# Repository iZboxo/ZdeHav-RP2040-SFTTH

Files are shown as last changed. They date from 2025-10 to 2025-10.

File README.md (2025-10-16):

# ZdeHav-RP2040-SFTTH
Stepper, fan, thermistor, thermistor and heater. Does it work? I don't know yet. But I hope so.

# What I know is wrong even now lol
BAV99W - has different mounting pads - one is meant for hand soldering, one for machine. Not a hard issue.
SK310A-TP D3, D4 - also different mounting style, this IS BAD. I missed this one. I only found 40V/0.3A schottky in 0603 - AND THATS NOT ENOUGH.

PCB
PCBdesign
Schematic1
Schematic2
PCBTop

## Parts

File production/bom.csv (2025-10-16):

Designator | Footprint | Quantity | Value | LCSC Part #
C1, C36, C4 | 0805 | 3 | 10u
C10, C8 | 0603 | 2 | 1u
C11, C12, C13, C14, C15, C16, C17, C20, C21, C28, C29, C30, C31, C32, C51, C6, C7, C9 | 0603 | 18 | 100n
C18 | CAPAE830X1050N | 1 | 100u
C19 | 1206 | 1 | 10u
C2, C3 | 0603 | 2 | 15p
C22 | 0603 | 1 | 4.7u
C23, C25, C26, C27 | 0603 | 4 | 1n
C24 | 0603 | 1 | 22n
C33, C34 | 0603 | 2 | 22u
C35 | 0603 | 1 | 10u
C5 | 0603 | 1 | C
D1 | SOT-323_SC-70_Handsoldering | 1 | BAV99W
D2, D5 | 0603 | 2 | LED
D3, D4 | 0603 | 2 | SK310A-TP
D6 | D_SOD-523 | 1 | BAT54KFILM
D7 | SOT-323_SC-70 | 1 | BAV99W
IC1 | AP63205WU7 | 1 | AP63205WU-7
J1 | USB421603A | 1 | USB4216-03-A
J10, J2, J9 | PinHeader_1x02_P2.54mm_Vertical | 3 | Conn_01x02
J11 | PinSocket_2x20_P2.54mm_Vertical | 1 | Conn_02x20_Odd_Even
J3 | SHDR4W97P0X254_1X4_1271X660X1143P | 1 | Conn_01x04
J4 | SHDR2W99P0X500_1X2_1001X762X1001P | 1 | 8718
J5, J6 | SHDR2W64P0X254_1X2_737X660X1181P | 2 | Conn_01x02
J7 | SHDR2W99P0X500_1X2_1001X762X1001P | 1 | Conn_01x02
J8 | RHDR3W64P0X254_1X3_1017X660X1194P | 1 | Conn_01x03
L1, L2, L3, L4, L5 | 0603 | 5 | BLM18KG121TN1D
L6 | L_APV_APH0530 | 1 | 6.8u
Q1 | TO-220-3_Horizontal_TabDown | 1 | IRLZ34NPBF
Q2 | SOT-23-3 | 1 | SI2342DS-T1-BE3
R1, R10, R5 | 0603 | 3 | 1k
R11, R14, R15 | 0603 | 3 | 4k7
R12, R13 | 0603 | 2 | 2k37
R16 | 0603 | 1 | 10k
R17, R19 | 0603 | 2 | 100k
R18 | 0603 | 1 | 2k2
R2 | 0603 | 1 | DNF
R20, R21 | 0603 | 2 | 1k8
R3, R4 | 0603 | 2 | 27.4
R6, R7 | 1206 | 2 | 22mili
R8, R9 | 0603 | 2 | 5k1
TH1 | 0402 | 1 | NTCG104LH104JTDS
U1 | QFN-56-1EP_7x7mm_P0.4mm_EP3.2x3.2mm | 1 | RP2040
U2 | SOT-223-3_TabPin2 | 1 | NCP1117-3.3_SOT223
U3 | SOIC-8_5.3x5.3mm_P1.27mm | 1 | W25Q128JVS
U4 | VQFN-28-1EP_5x5mm_P0.5mm_EP3.7x3.7mm_ThermalVias | 1 | TMC2209-LA
Y1 | Crystal_SMD_Abracon_ABM8G-4Pin_3.2x2.5mm | 1 | ABM8-272-T3

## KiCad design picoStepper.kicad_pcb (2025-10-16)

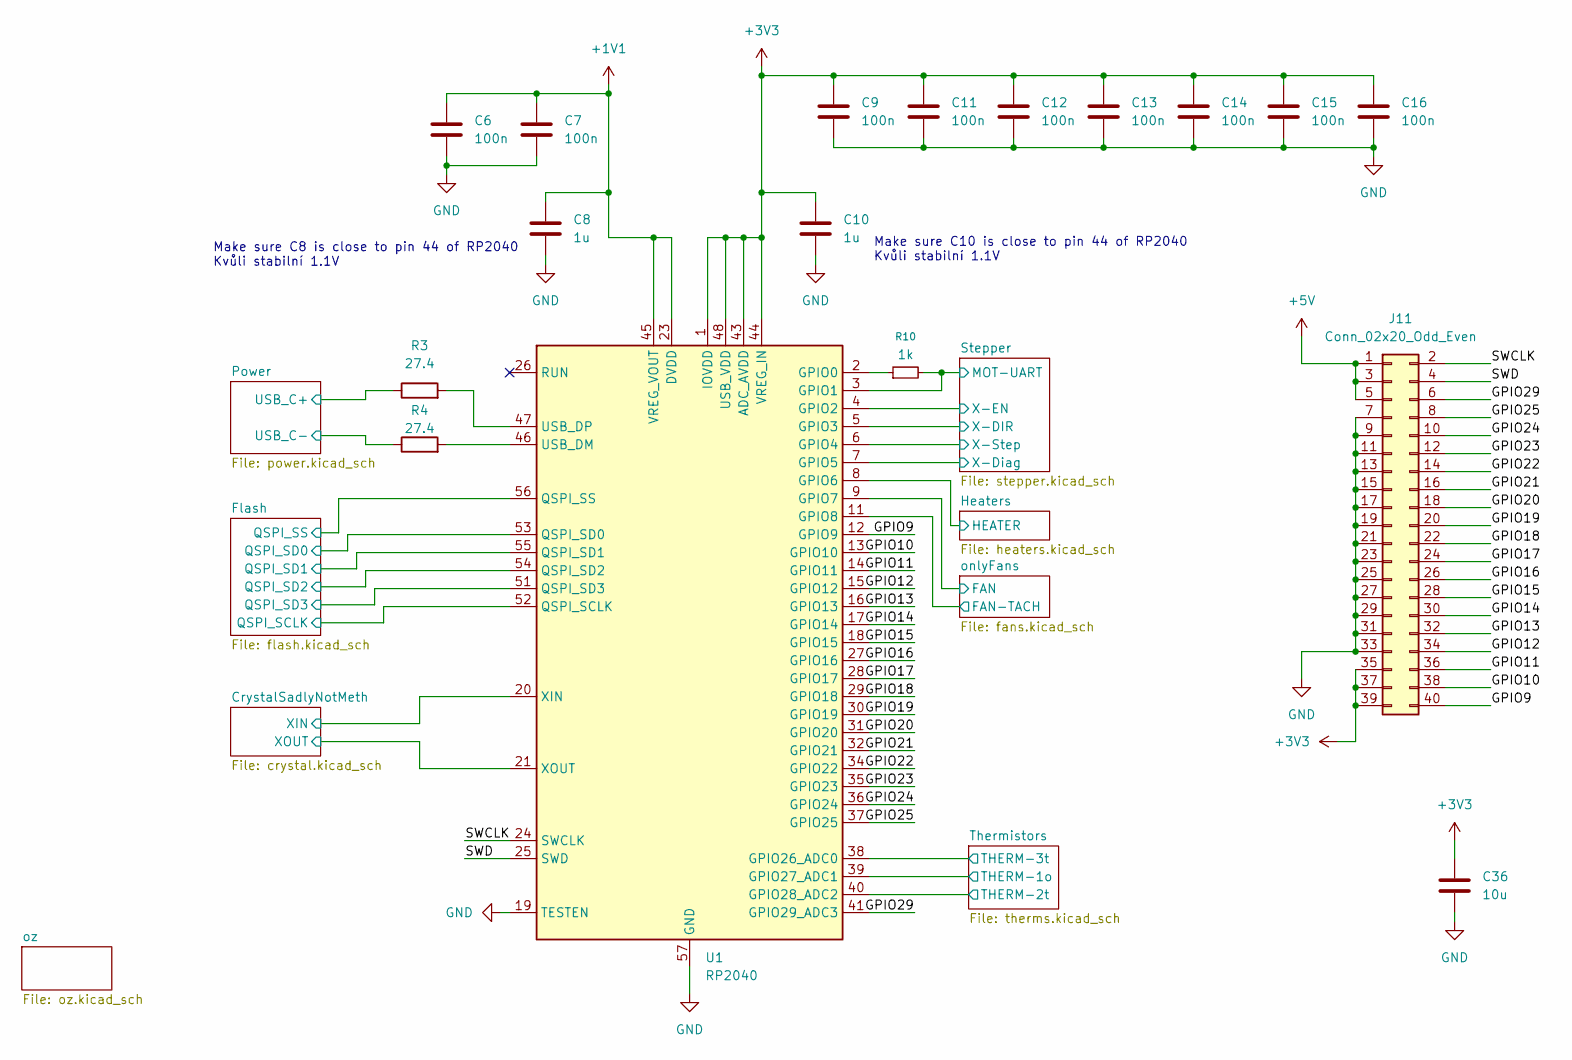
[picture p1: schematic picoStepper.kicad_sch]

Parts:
C6, C7, C9, C11, C12, C13, C14, C15, C16: 100n; C_0603_1608Metric_Pad1.08x0.95mm_HandSolder
C8, C10: 1u; C_0603_1608Metric_Pad1.08x0.95mm_HandSolder
C36: 10u; C_0805_2012Metric_Pad1.18x1.45mm_HandSolder
J11: Conn_02x20_Odd_Even; PinSocket_2x20_P2.54mm_Vertical
R3, R4: 27.4; R_0603_1608Metric_Pad0.98x0.95mm_HandSolder
R10: 1k; R_0603_1608Metric_Pad0.98x0.95mm_HandSolder
U1: RP2040; QFN-56-1EP_7x7mm_P0.4mm_EP3.2x3.2mm

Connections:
+1V1: C6.1, C7.1, C8.1, U1.23 (DVDD), U1.45 (VREG_VOUT), U1.50 (DVDD)
+3V3: C9.1, C10.1, C11.1, C12.1, C13.1, C14.1, C15.1, C16.1, C36.1, J11.35, J11.37, J11.39, U1.1 (IOVDD), U1.10 (IOVDD), U1.22 (IOVDD), U1.33 (IOVDD), U1.42 (IOVDD), U1.43 (ADC_AVDD), U1.44 (VREG_IN), U1.48 (USB_VDD), U1.49 (IOVDD); also elsewhere on the board
+5V: J11.1, J11.3, J11.5; also elsewhere on the board
/CrystalSadlyNotMeth/XIN: U1.20 (XIN); also elsewhere on the board
/CrystalSadlyNotMeth/XOUT: U1.21 (XOUT); also elsewhere on the board
/Flash/QSPI_SCLK: U1.52 (QSPI_SCLK); also elsewhere on the board
/Flash/QSPI_SD0: U1.53 (QSPI_SD0); also elsewhere on the board
/Flash/QSPI_SD1: U1.55 (QSPI_SD1); also elsewhere on the board
/Flash/QSPI_SD2: U1.54 (QSPI_SD2); also elsewhere on the board
/Flash/QSPI_SD3: U1.51 (QSPI_SD3); also elsewhere on the board
/Flash/QSPI_SS: U1.56 (QSPI_SS); also elsewhere on the board
/GPIO9: J11.40, U1.12 (GPIO9)
/GPIO10: J11.38, U1.13 (GPIO10)
/GPIO11: J11.36, U1.14 (GPIO11)
/GPIO12: J11.34, U1.15 (GPIO12)
/GPIO13: J11.32, U1.16 (GPIO13)
/GPIO14: J11.30, U1.17 (GPIO14)
/GPIO15: J11.28, U1.18 (GPIO15)
/GPIO16: J11.26, U1.27 (GPIO16)
/GPIO17: J11.24, U1.28 (GPIO17)
/GPIO18: J11.22, U1.29 (GPIO18)
/GPIO19: J11.20, U1.30 (GPIO19)
/GPIO20: J11.18, U1.31 (GPIO20)
/GPIO21: J11.16, U1.32 (GPIO21)
/GPIO22: J11.14, U1.34 (GPIO22)
/GPIO23: J11.12, U1.35 (GPIO23)
/GPIO24: J11.10, U1.36 (GPIO24)
/GPIO25: J11.8, U1.37 (GPIO25)
/GPIO29: J11.6, U1.41 (GPIO29_ADC3)
/Heaters/HEATER: U1.8 (GPIO6); also elsewhere on the board
/Power/USB_C+: R3.1; also elsewhere on the board
/Power/USB_C-: R4.1; also elsewhere on the board
/SWCLK: J11.2, U1.24 (SWCLK)
/SWD: J11.4, U1.25 (SWD)
/Stepper/MOT-UART: R10.2, U1.3 (GPIO1); also elsewhere on the board
/Stepper/X-DIR: U1.5 (GPIO3); also elsewhere on the board
/Stepper/X-Diag: U1.7 (GPIO5); also elsewhere on the board
/Stepper/X-EN: U1.4 (GPIO2); also elsewhere on the board
/Stepper/X-Step: U1.6 (GPIO4); also elsewhere on the board
/Thermistors/THERM-1o: U1.39 (GPIO27_ADC1); also elsewhere on the board
/Thermistors/THERM-2t: U1.40 (GPIO28_ADC2); also elsewhere on the board
/Thermistors/THERM-3t: U1.38 (GPIO26_ADC0); also elsewhere on the board
/onlyFans/FAN: U1.9 (GPIO7); also elsewhere on the board
/onlyFans/FAN-TACH: U1.11 (GPIO8); also elsewhere on the board
GND: C6.2, C7.2, C8.2, C9.2, C10.2, C11.2, C12.2, C13.2, C14.2, C15.2, C16.2, C36.2, J11.7, J11.9, J11.11, J11.13, J11.15, J11.17, J11.19, J11.21, J11.23, J11.25, J11.27, J11.29, J11.31, J11.33, U1.19 (TESTEN), U1.57 (GND); also elsewhere on the board
unnamed: R10.1, U1.2 (GPIO0)
unnamed: R4.2, U1.46 (USB_DM)
unnamed: R3.2, U1.47 (USB_DP)

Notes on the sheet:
Make sure C10 is close to pin 44 of RP2040 Kvůli stabilní 1.1V
Make sure C8 is close to pin 44 of RP2040 Kvůli stabilní 1.1V

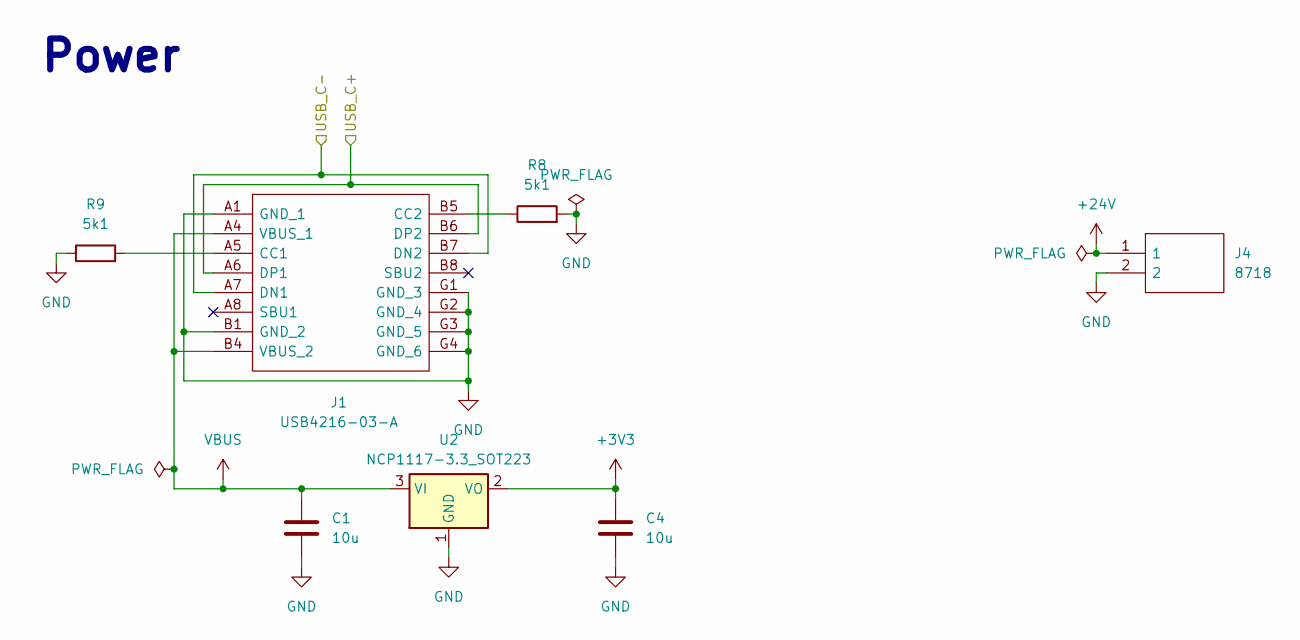
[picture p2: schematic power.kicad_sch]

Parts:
C1, C4: 10u; C_0805_2012Metric_Pad1.18x1.45mm_HandSolder
J1: USB4216-03-A; USB421603A; Mouser Part Number 640-USB4216-03-A
J4: 8718; SHDR2W99P0X500_1X2_1001X762X1001P; Mouser Part Number 534-8718
R8, R9: 5k1; R_0603_1608Metric_Pad0.98x0.95mm_HandSolder
U2: NCP1117-3.3_SOT223; SOT-223-3_TabPin2

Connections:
+3V3: C4.1, U2.2 (VO); also elsewhere on the board
+24V: J4.1; also elsewhere on the board
/Power/USB_C+: J1.A6 (DP1), J1.B6 (DP2); also elsewhere on the board
/Power/USB_C-: J1.A7 (DN1), J1.B7 (DN2); also elsewhere on the board
GND: C1.2, C4.2, J1.A1 (GND_1), J1.B1 (GND_2), J1.G1 (GND_3), J1.G2 (GND_4), J1.G3 (GND_5), J1.G4 (GND_6), J4.2, R8.2, R9.1, U2.1 (GND); also elsewhere on the board
unnamed: J1.A5 (CC1), R9.2
unnamed: J1.B5 (CC2), R8.1
VBUS: C1.1, J1.A4 (VBUS_1), J1.B4 (VBUS_2), U2.3 (VI)

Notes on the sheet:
Power

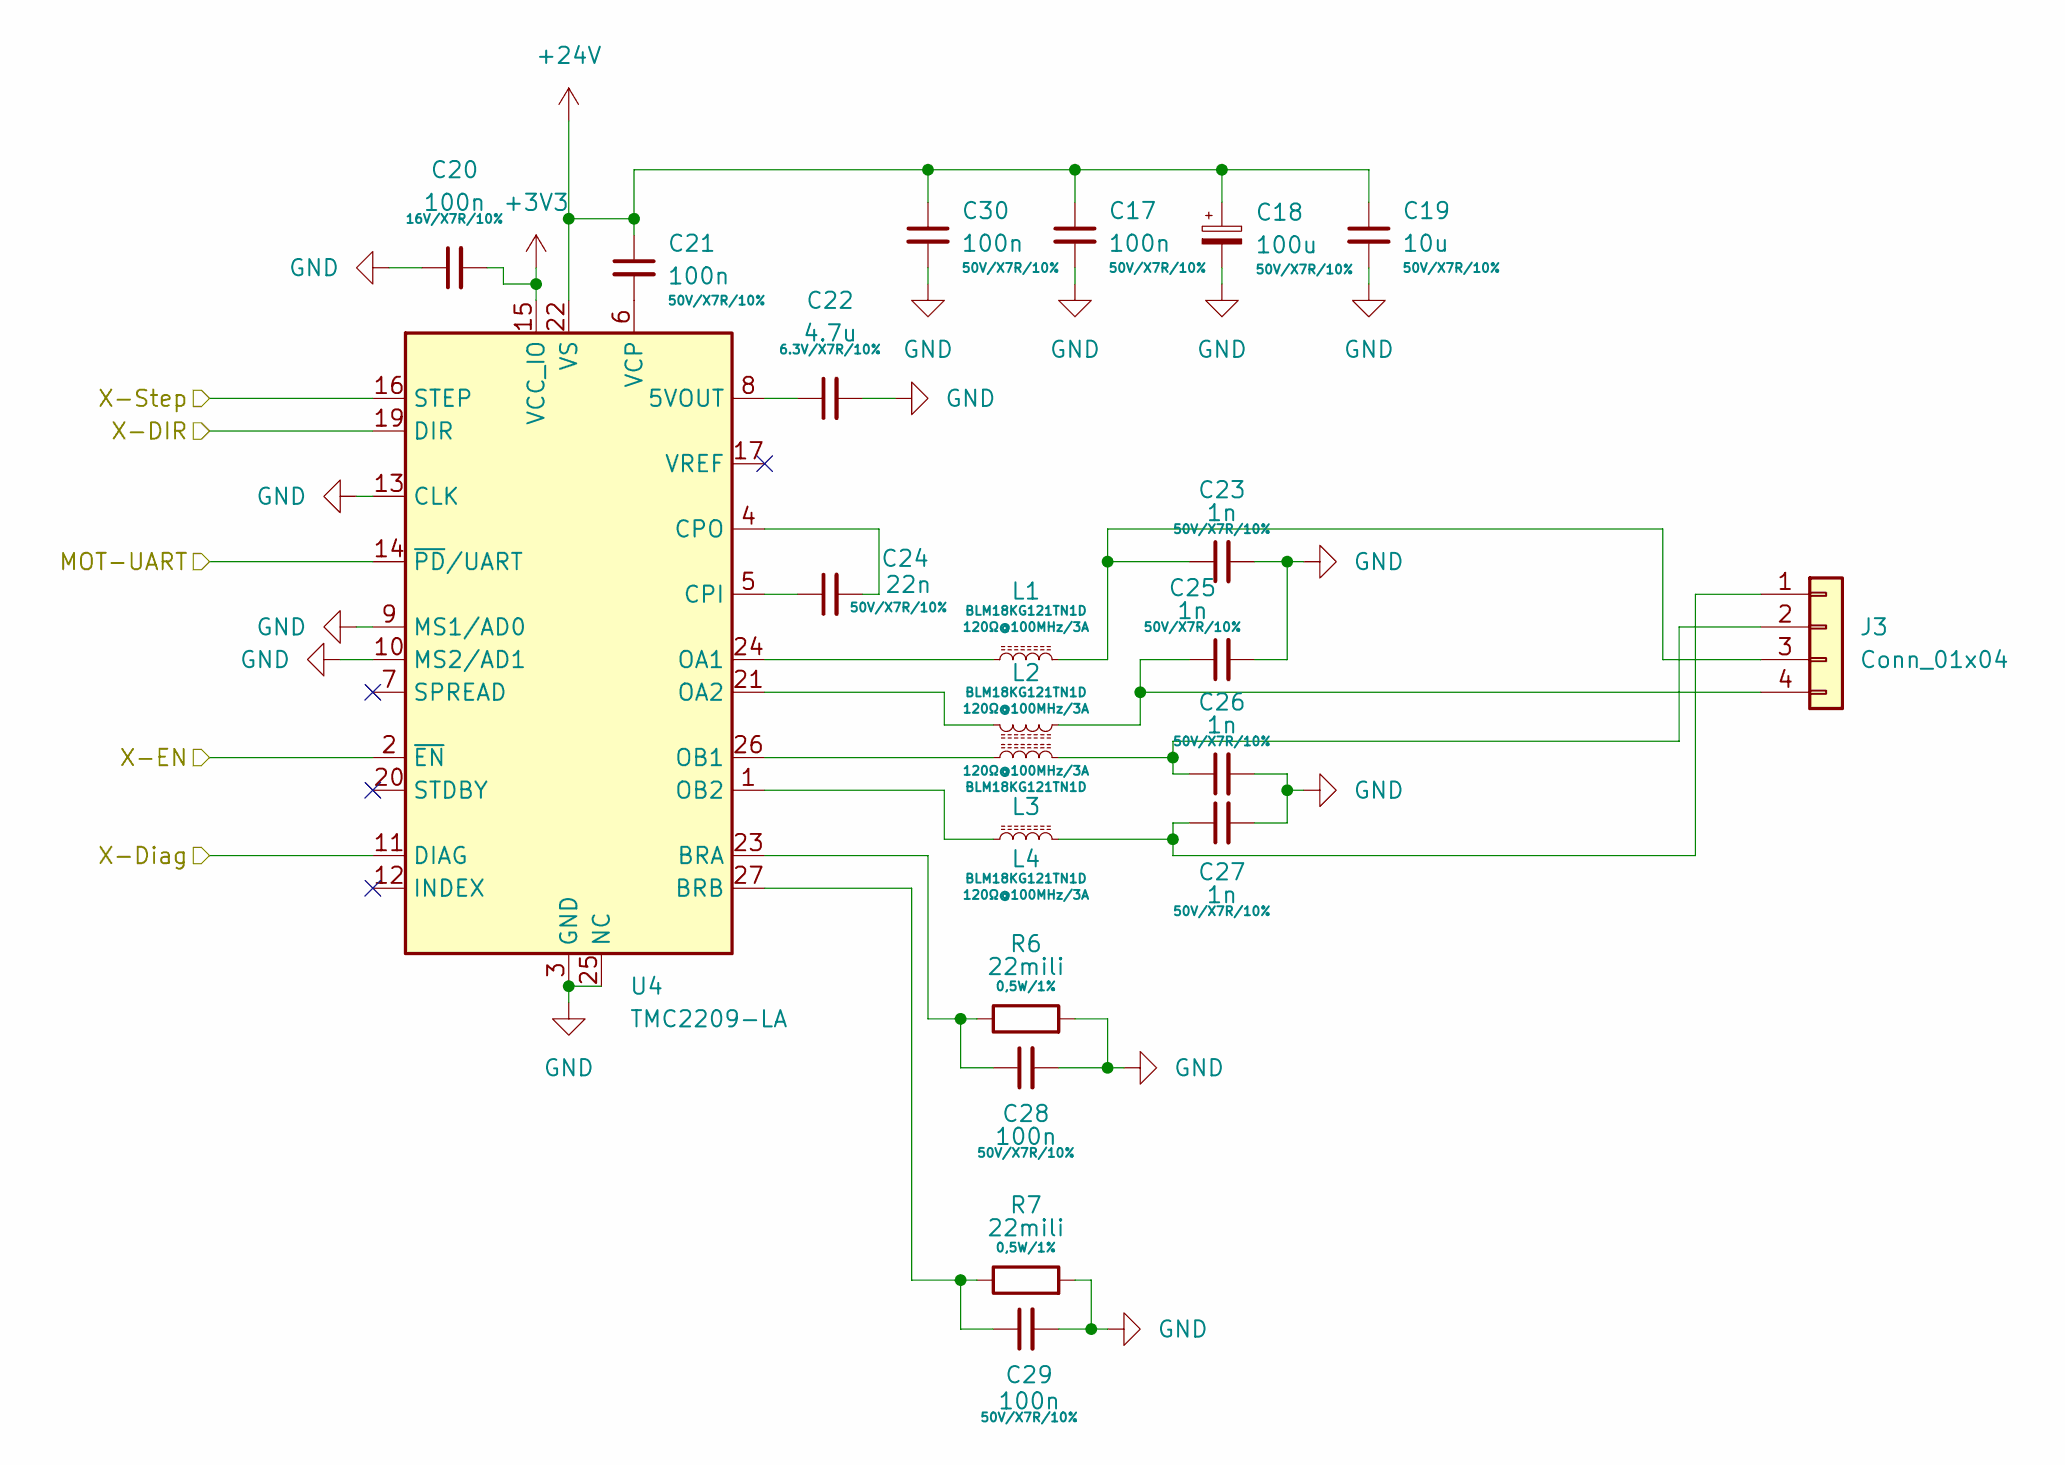
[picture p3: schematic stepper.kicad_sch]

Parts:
C17, C20, C21, C28, C29, C30: 100n; C_0603_1608Metric_Pad1.08x0.95mm_HandSolder
C18: 100u; CAPAE830X1050N
C19: 10u; C_1206_3216Metric_Pad1.33x1.80mm_HandSolder
C22: 4.7u; C_0603_1608Metric_Pad1.08x0.95mm_HandSolder
C23, C25, C26, C27: 1n; C_0603_1608Metric_Pad1.08x0.95mm_HandSolder
C24: 22n; C_0603_1608Metric_Pad1.08x0.95mm_HandSolder
J3: Conn_01x04; SHDR4W97P0X254_1X4_1271X660X1143P
L1, L2, L3, L4: BLM18KG121TN1D; D_0603_1608Metric_Pad1.05x0.95mm_HandSolder
R6, R7: 22mili; R_1206_3216Metric_Pad1.30x1.75mm_HandSolder
U4: TMC2209-LA; VQFN-28-1EP_5x5mm_P0.5mm_EP3.7x3.7mm_ThermalVias

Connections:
+3V3: C20.2, U4.15 (VCC_IO); also elsewhere on the board
+24V: C17.1, C18.1, C19.1, C21.1, C30.1, U4.22 (VS), U4.28 (VS); also elsewhere on the board
/Stepper/MOT-UART: U4.14 (~PD/UART); also elsewhere on the board
/Stepper/X-DIR: U4.19 (DIR); also elsewhere on the board
/Stepper/X-Diag: U4.11 (DIAG); also elsewhere on the board
/Stepper/X-EN: U4.2 (~EN); also elsewhere on the board
/Stepper/X-Step: U4.16 (STEP); also elsewhere on the board
GND: C17.2, C18.2, C19.2, C20.1, C22.2, C23.2, C25.2, C26.2, C27.2, C28.2, C29.2, C30.2, R6.2, R7.2, U4.3 (GND), U4.9 (MS1/AD0), U4.10 (MS2/AD1), U4.13 (CLK), U4.18 (GND), U4.25 (NC), U4.29 (GND); also elsewhere on the board
unnamed: C27.1, J3.1, L4.2
unnamed: C26.1, J3.2, L3.2
unnamed: C23.1, J3.3, L1.2
unnamed: C25.1, J3.4, L2.1
unnamed: C22.1, U4.8 (5VOUT)
unnamed: C28.1, R6.1, U4.23 (BRA)
unnamed: C29.1, R7.1, U4.27 (BRB)
unnamed: C24.1, U4.5 (CPI)
unnamed: C24.2, U4.4 (CPO)
unnamed: L1.1, U4.24 (OA1)
unnamed: L2.2, U4.21 (OA2)
unnamed: L3.1, U4.26 (OB1)
unnamed: L4.1, U4.1 (OB2)
unnamed: C21.2, U4.6 (VCP)

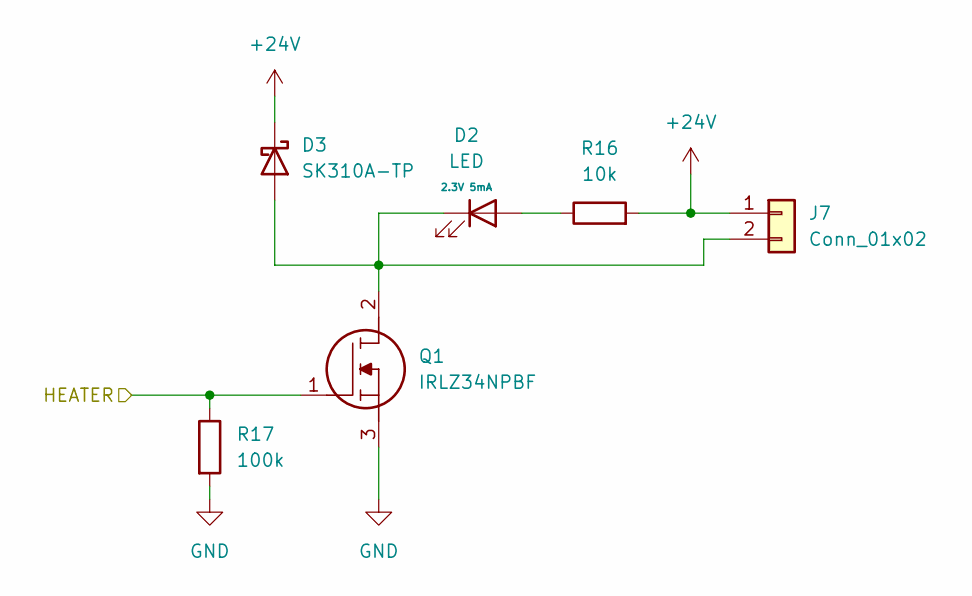
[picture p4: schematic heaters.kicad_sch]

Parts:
D2: LED; D_0603_1608Metric_Pad1.05x0.95mm_HandSolder
D3: SK310A-TP; D_0603_1608Metric_Pad1.05x0.95mm_HandSolder
J7: Conn_01x02; SHDR2W99P0X500_1X2_1001X762X1001P
Q1: IRLZ34NPBF; TO-220-3_Horizontal_TabDown; Mouser Part Number 942-IRLZ34NPBF
R16: 10k; R_0603_1608Metric_Pad0.98x0.95mm_HandSolder
R17: 100k; R_0603_1608Metric_Pad0.98x0.95mm_HandSolder

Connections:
+24V: D3.1 (K), J7.1, R16.2; also elsewhere on the board
/Heaters/HEATER: Q1.1, R17.1; also elsewhere on the board
GND: Q1.3, R17.2; also elsewhere on the board
unnamed: D2.2 (A), R16.1
unnamed: D2.1 (K), D3.2 (A), J7.2, Q1.2

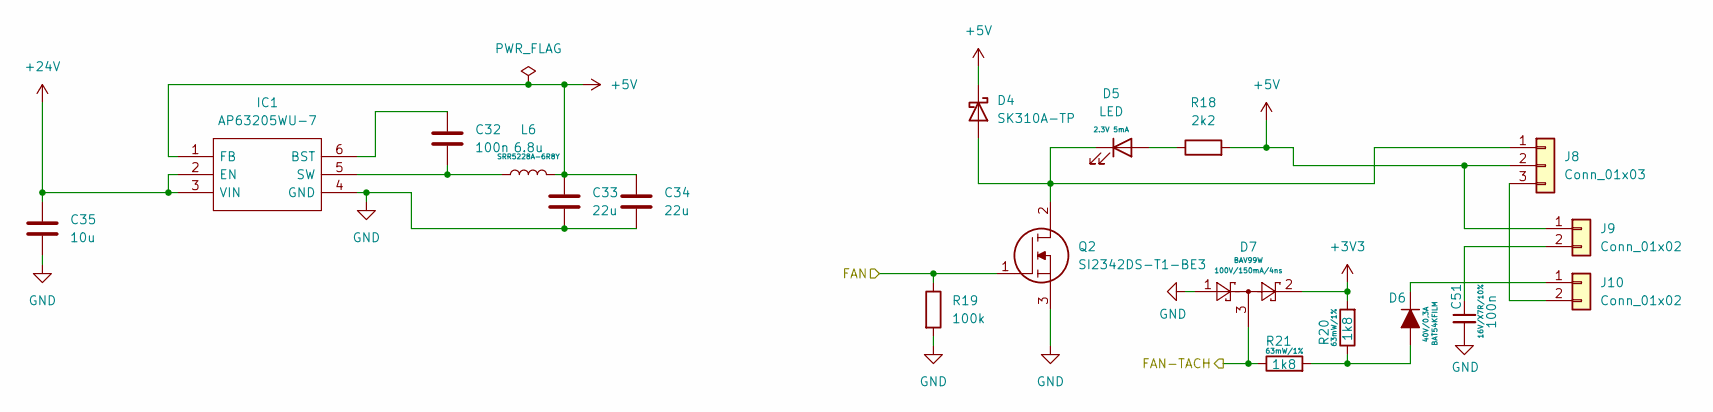
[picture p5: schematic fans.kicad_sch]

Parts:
C32, C51: 100n; C_0603_1608Metric_Pad1.08x0.95mm_HandSolder
C33, C34: 22u; C_0603_1608Metric_Pad1.08x0.95mm_HandSolder
C35: 10u; C_0603_1608Metric_Pad1.08x0.95mm_HandSolder
D4: SK310A-TP; D_0603_1608Metric_Pad1.05x0.95mm_HandSolder
D5: LED; D_0603_1608Metric_Pad1.05x0.95mm_HandSolder
D6: BAT54KFILM; D_SOD-523
D7: BAV99W; SOT-323_SC-70
IC1: AP63205WU-7; AP63205WU7; Mouser Part Number 621-AP63205WU-7
J8: Conn_01x03; RHDR3W64P0X254_1X3_1017X660X1194P
J9, J10: Conn_01x02; PinHeader_1x02_P2.54mm_Vertical
L6: 6.8u; L_APV_APH0530
Q2: SI2342DS-T1-BE3; SOT-23-3; Mouser Part Number 942-IRLZ34NPBF
R18: 2k2; R_0603_1608Metric_Pad0.98x0.95mm_HandSolder
R19: 100k; R_0603_1608Metric_Pad0.98x0.95mm_HandSolder
R20, R21: 1k8; R_0603_1608Metric_Pad0.98x0.95mm_HandSolder

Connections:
+3V3: D7.2, R20.2; also elsewhere on the board
+5V: C33.1, C34.1, D4.1 (K), IC1.1 (FB), J8.2, J9.1, L6.2, R18.2; also elsewhere on the board
+24V: C35.1, IC1.2 (EN), IC1.3 (VIN); also elsewhere on the board
/onlyFans/FAN: Q2.1, R19.1; also elsewhere on the board
/onlyFans/FAN-TACH: D7.3, R21.1; also elsewhere on the board
GND: C33.2, C34.2, C35.2, C51.2, D7.1, IC1.4 (GND), Q2.3, R19.2; also elsewhere on the board
unnamed: D4.2 (A), D5.1 (K), J8.1, Q2.2
unnamed: D5.2 (A), R18.1
unnamed: D6.2 (A), R20.1, R21.2
unnamed: D6.1 (K), J10.1
unnamed: C32.1, IC1.6 (BST)
unnamed: C32.2, IC1.5 (SW), L6.1
unnamed: C51.1, J9.2
unnamed: J8.3, J10.2

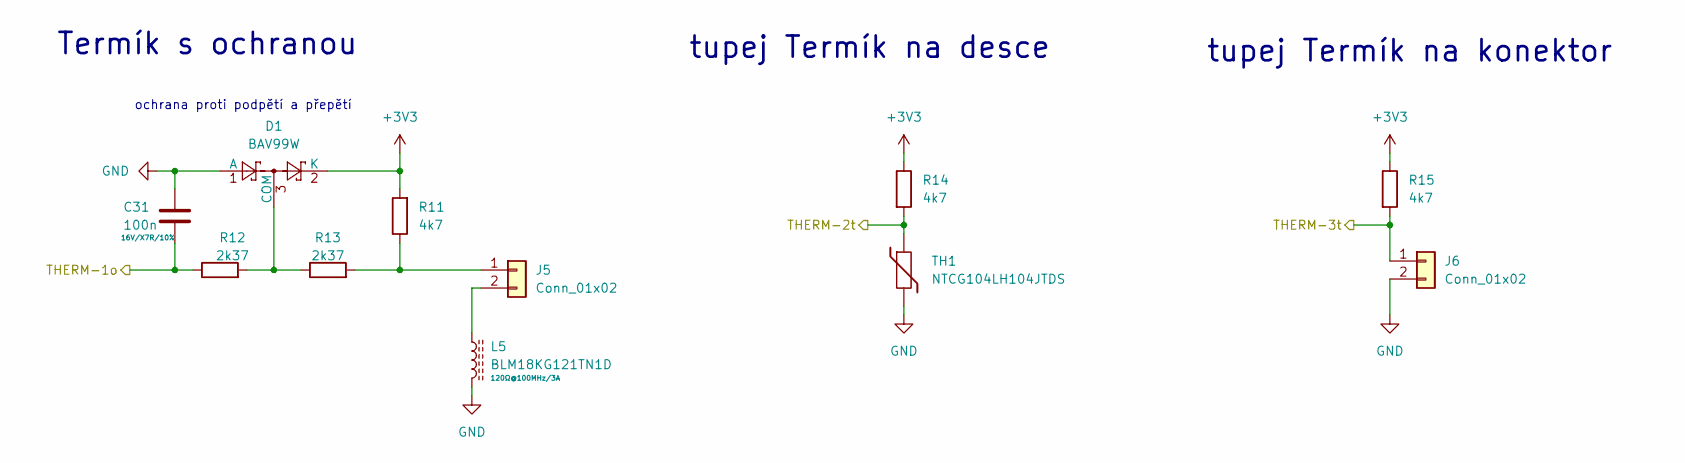
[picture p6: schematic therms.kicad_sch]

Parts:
C31: 100n; C_0603_1608Metric_Pad1.08x0.95mm_HandSolder
D1: BAV99W; SOT-323_SC-70_Handsoldering
J5, J6: Conn_01x02; SHDR2W64P0X254_1X2_737X660X1181P
L5: BLM18KG121TN1D; D_0603_1608Metric_Pad1.05x0.95mm_HandSolder
R11, R14, R15: 4k7; R_0603_1608Metric_Pad0.98x0.95mm_HandSolder
R12, R13: 2k37; R_0603_1608Metric_Pad0.98x0.95mm_HandSolder
TH1: NTCG104LH104JTDS; R_0402_1005Metric_Pad0.72x0.64mm_HandSolder

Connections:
+3V3: D1.2 (K), R11.2, R14.1, R15.1; also elsewhere on the board
/Thermistors/THERM-1o: C31.2, R12.1; also elsewhere on the board
/Thermistors/THERM-2t: R14.2, TH1.1; also elsewhere on the board
/Thermistors/THERM-3t: J6.1, R15.2; also elsewhere on the board
GND: C31.1, D1.1 (A), J6.2, L5.2, TH1.2; also elsewhere on the board
unnamed: D1.3 (COM), R12.2, R13.1
unnamed: J5.1, R11.1, R13.2
unnamed: J5.2, L5.1

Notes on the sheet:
ochrana proti podpětí a přepětí
tupej Termík na konektor
Termík s ochranou
tupej Termík na desce

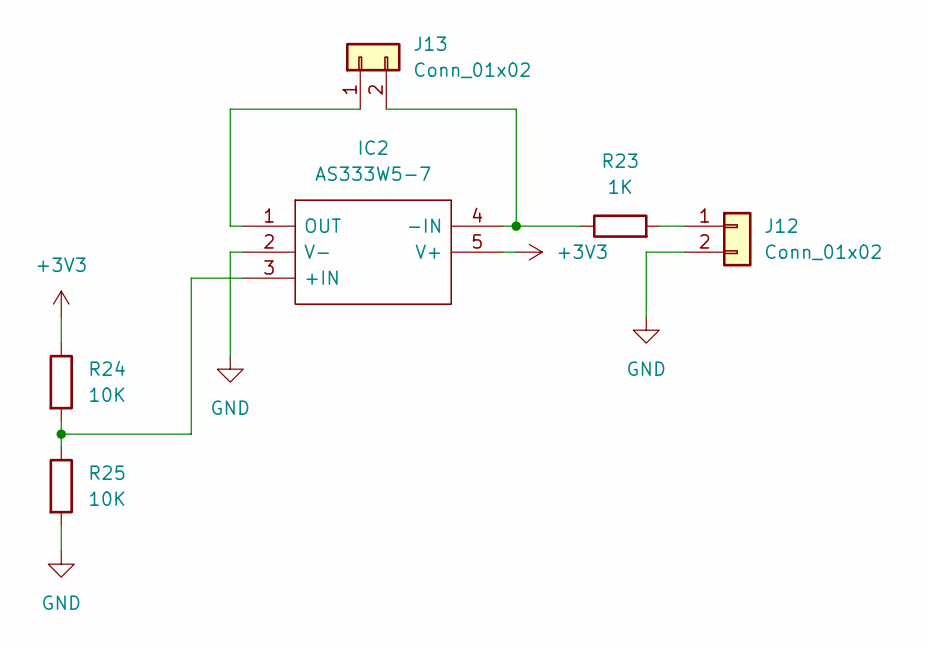
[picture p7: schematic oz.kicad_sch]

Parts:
IC2: AS333W5-7; SOT95P285X140-5N; Mouser Part Number 621-AS333W5-7
J12, J13: Conn_01x02; PinHeader_1x02_P2.54mm_Vertical
R23: 1K; R_0603_1608Metric_Pad0.98x0.95mm_HandSolder
R24, R25: 10K; R_0603_1608Metric_Pad0.98x0.95mm_HandSolder

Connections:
unnamed: IC2.1 (OUT), J13.1
unnamed: IC2.2 (V-), J12.2, R25.2
unnamed: IC2.3 (+IN), R24.2, R25.1
unnamed: IC2.4 (-IN), J13.2, R23.1
unnamed: IC2.5 (V+), R24.1
unnamed: J12.1, R23.2

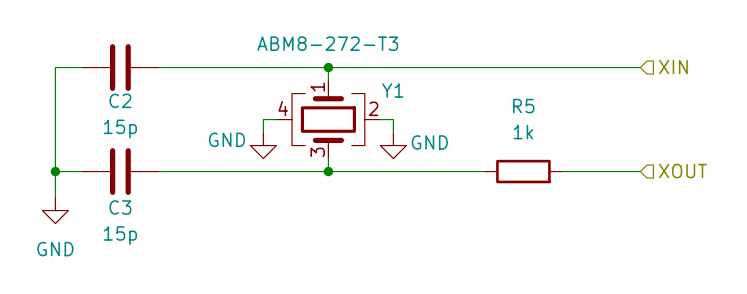
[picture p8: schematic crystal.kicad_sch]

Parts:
C2, C3: 15p; C_0603_1608Metric_Pad1.08x0.95mm_HandSolder
R5: 1k; R_0603_1608Metric_Pad0.98x0.95mm_HandSolder
Y1: ABM8-272-T3; Crystal_SMD_Abracon_ABM8G-4Pin_3.2x2.5mm

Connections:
/CrystalSadlyNotMeth/XIN: C2.2, Y1.1; also elsewhere on the board
/CrystalSadlyNotMeth/XOUT: R5.2; also elsewhere on the board
GND: C2.1, C3.1, Y1.2, Y1.4; also elsewhere on the board
unnamed: C3.2, R5.1, Y1.3

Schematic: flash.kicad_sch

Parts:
C5: C; C_0603_1608Metric_Pad1.08x0.95mm_HandSolder
J2: Conn_01x02; PinHeader_1x02_P2.54mm_Vertical
R1: 1k; R_0603_1608Metric_Pad0.98x0.95mm_HandSolder
R2: DNF; R_0603_1608Metric_Pad0.98x0.95mm_HandSolder
U3: W25Q128JVS; SOIC-8_5.3x5.3mm_P1.27mm

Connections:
+3V3: C5.1, R2.1, U3.8 (VCC); also elsewhere on the board
/Flash/QSPI_SCLK: U3.6 (CLK); also elsewhere on the board
/Flash/QSPI_SD0: U3.5 (DI/IO_{0}); also elsewhere on the board
/Flash/QSPI_SD1: U3.2 (DO/IO_{1}); also elsewhere on the board
/Flash/QSPI_SD2: U3.3 (~WP/IO_{2}); also elsewhere on the board
/Flash/QSPI_SD3: U3.7 (~HOLD/~RESET/IO_{3}); also elsewhere on the board
/Flash/QSPI_SS: R1.2, R2.2, U3.1 (~CS); also elsewhere on the board
GND: C5.2, J2.1, U3.4 (GND); also elsewhere on the board
unnamed: J2.2, R1.1

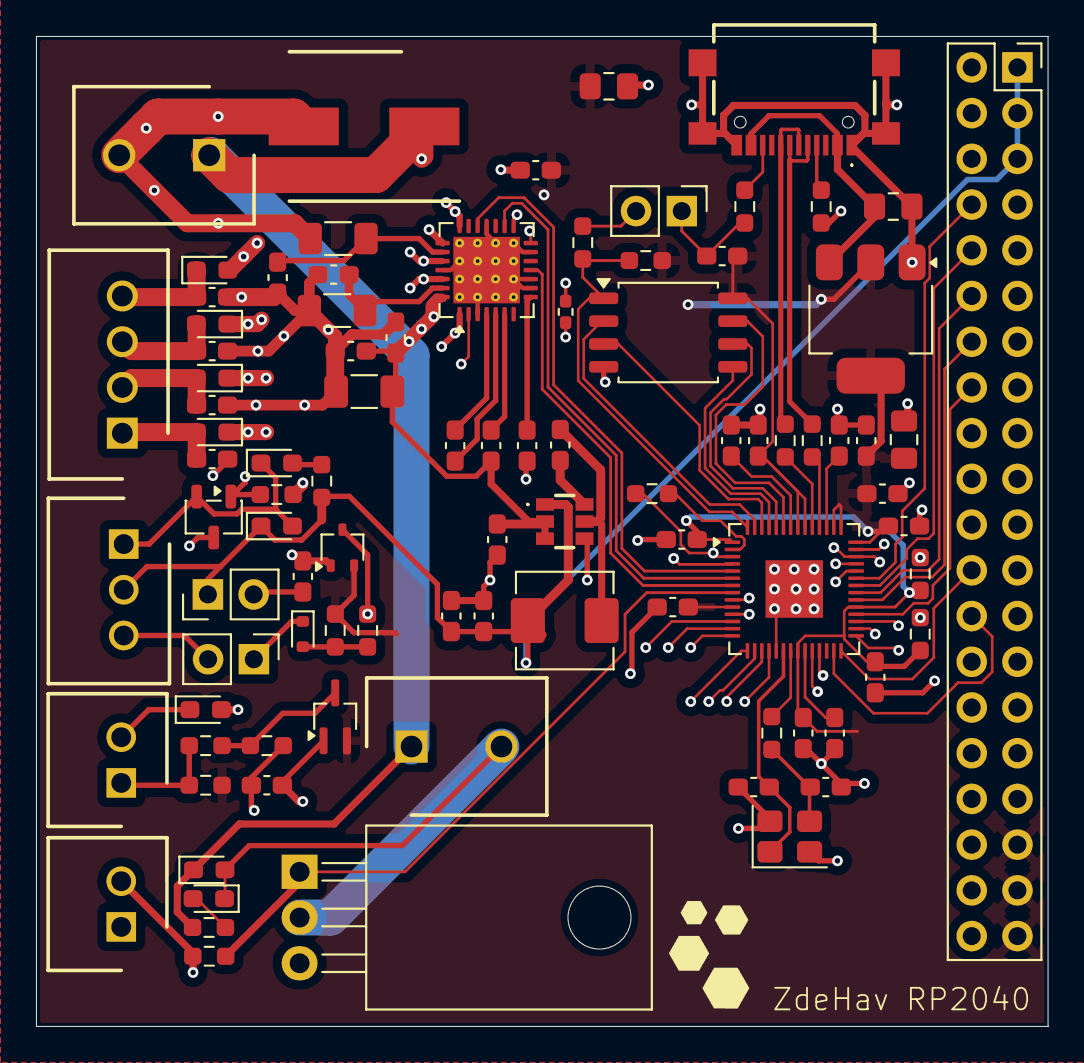
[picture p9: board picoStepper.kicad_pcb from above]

Board: 4 copper layers, 56.2 x 55.0 mm, 91 parts (0 on the bottom side), 81 nets.
